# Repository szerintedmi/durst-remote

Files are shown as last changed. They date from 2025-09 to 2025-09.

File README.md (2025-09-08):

# Durst Laborator 1200 — Wireless Display and Control

Retrofitted display and control for the Durst Laborator 1200 enlarger.

Controls:

- Motor up/down (normal or fast)
- Lens up/down (normal or fast)
- Lamp on/off or by timer

Control via:

- TM1638 panel (8 buttons)
- Bluetooth gamepad

Displays:

- TM1638 7‑segment
- Grove LCD (16×2 characters)

Either display can be wired to the master module or used wirelessly via a slave node over ESP‑NOW. The device also starts its own Wi‑Fi access point for setup, so you don’t need to join home Wi‑Fi to use the wireless display/panel.

## Overview

- Master node drives motors, lamp SSR, UI, and broadcasts display over ESP‑NOW.
- Slave node (optional) only renders the broadcasted display on TM1638/LCD.
- Brightness values: 0,1,2,7,OFF(255), persisted to NVS.

## Hardware/Pins (ESP32)

- TM1638: `STB=13`, `CLK=32`, `DIO=14` (high‑freq mode enabled).
- Buzzer: `GPIO16` (LEDC ch 4). Indicator LED disabled.
- Lamp SSR: `GPIO33`.
- Motor 1 (DRV8874): `IN1=25`, `IN2=26`, `CS=35`, `FAULT=27`, `SLEEP` tied HIGH, LEDC ch `0/1`.
- Motor 2 (DRV8874): `IN1=18`, `IN2=19`, `CS=34`, `FAULT=22`, `SLEEP` tied HIGH, LEDC ch `2/3`.

## Wiring

- Diagram: [KiCad/DurstControlRetrofitWiring.pdf](KiCad/DurstControlRetrofitWiring.pdf) or [KiCad/](KiCad/) (draft / work in progress) )
- For connecting the motors, the limit switches and lamp to the right cables see [Durst Service manuals](http://durst.loremi.com/).
- Slave node: same wiring concept; only one or both displays (TM1638 and/or Grove LCD) need to be connected.

## Controls

TM1638 panel (controls only if TM1638 is connected to master):

- `S1` Fast speed (motors or timer adjust)
- `S1+S8` toggle lamp (on/off)
- `S2` timer −0.1s; `S3` timer +0.1s
- `S1+S2` timer -1s; `S1+S3` timer +1s
- `S4` M1 down; `S5` M1 up
- `S6` M2 down; `S7` M2 up
- `S8` start / cancel timer
- Conflicts (e.g., up+down) coast + short beep.

Bluetooth gamepad (Bluepad32):

- `Cross(×)` / `Triangle(△)`: M1 (Head) up/down
- `Square(□)`  /  `Circle(○)` : M2 (Lens) up/down
- Fast motor Speed: `L2`/`R2`,  Insane `L1`
- Timer adjust +/-0.1s: D‑pad Up/Down
- Timer +/-1s: `L2`/`R2` + Dpad Up/Down
- Timer +/-10s: `L1` + Dpad Up/Down
- Start / cancel lamp with timer:  D-Pad Right
- Toggle lamp: D-Pad Left
- Adjust TM1638 Display Brightness: `R1`

## Display & Feedback

- TM1638 text shows the active motor duty or `ERRn`, plus lamp and timer (e.g., `123L  4.5`).
- LCD line 1/2 show a short status and timer; LEDs mirror the buttons mask.
- Display state is broadcast over ESP‑NOW; slaves render the same UI.

## Motor Driver (DRV8874)

- FreeRTOS tasks: duty control (500 Hz) and current sense averaging (up to 100 Hz).
- Active brake: both IN high for a short window, then coast.
- Min duty per direction allows asymmetric thresholds; ADC uses 11 dB attenuation.

## Buzzer

- LEDC‑based tone with one‑shot `esp_timer` auto‑stop. Used on conflict/fault.

## Wi‑Fi, ESP‑NOW & Web UI

- Starts SoftAP and attempts STA using saved creds.
- Endpoints: `GET /wifi/api/status`, `POST /wifi/save`, `POST /wifi/reset`.
- UI: `/index.html` (quick), `/wifi/index.html` (detailed+config).
- ESP‑NOW mesh is initialized; broadcast peer is pre‑added. Display messages use `MsgV1`.

## Build & Flash (PlatformIO)

- Master (default): `pio run -e esp32dev` → upload with `-t upload`.
- Slave (display‑only): `pio run -e esp32slave` → upload with `-t upload`.
- LittleFS: `pio run -t buildfs` and `pio run -t uploadfs`.

Notes: see [platformio.ini](platformio.ini) for board, ports, Bluepad32 framework package, and the pre‑build gzip step ([tools/gzip_fs.py](tools/gzip_fs.py)).

## Repo Layout

- [src/](src/) — [mainMaster.cpp](src/mainMaster.cpp) (master), [mainSlave.cpp](src/mainSlave.cpp) (slave).
- [lib/DRV8874/](lib/DRV8874/) — motor driver and control tasks.
- [lib/Controls/](lib/Controls/), [lib/GamePad/](lib/GamePad/) — input merge and Bluepad32 wrapper.
- [lib/DisplayMux/](lib/DisplayMux/), [lib/TM1638plusWrapper/](lib/TM1638plusWrapper/) — display + broadcast.
- [lib/WifiPortal/](lib/WifiPortal/) — SoftAP/STA, routes, ESP‑NOW init.
- [data_src/](data_src/) → [data/](data/) — web UI, gzipped at build.

## Mesh Password

- default password used for the mesh SoftAP is `changeme`
- Create `include/secrets.h` in [include/](include/) and add `#define MESH_PASS yourpassword` to customize.
- `include/secrets.h` is already in [.gitignore](.gitignore)

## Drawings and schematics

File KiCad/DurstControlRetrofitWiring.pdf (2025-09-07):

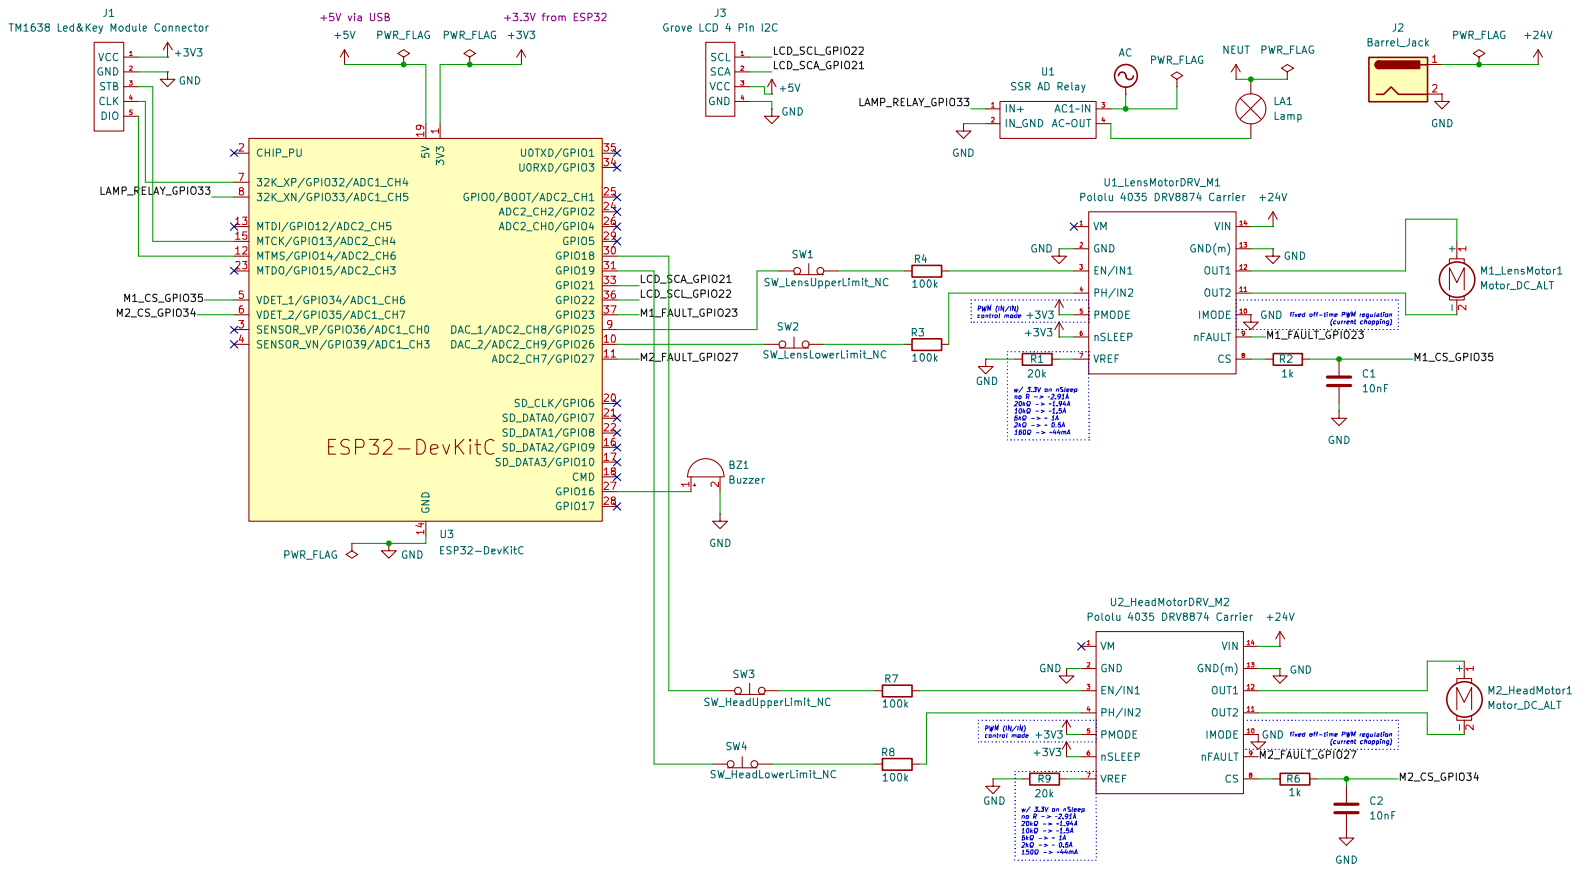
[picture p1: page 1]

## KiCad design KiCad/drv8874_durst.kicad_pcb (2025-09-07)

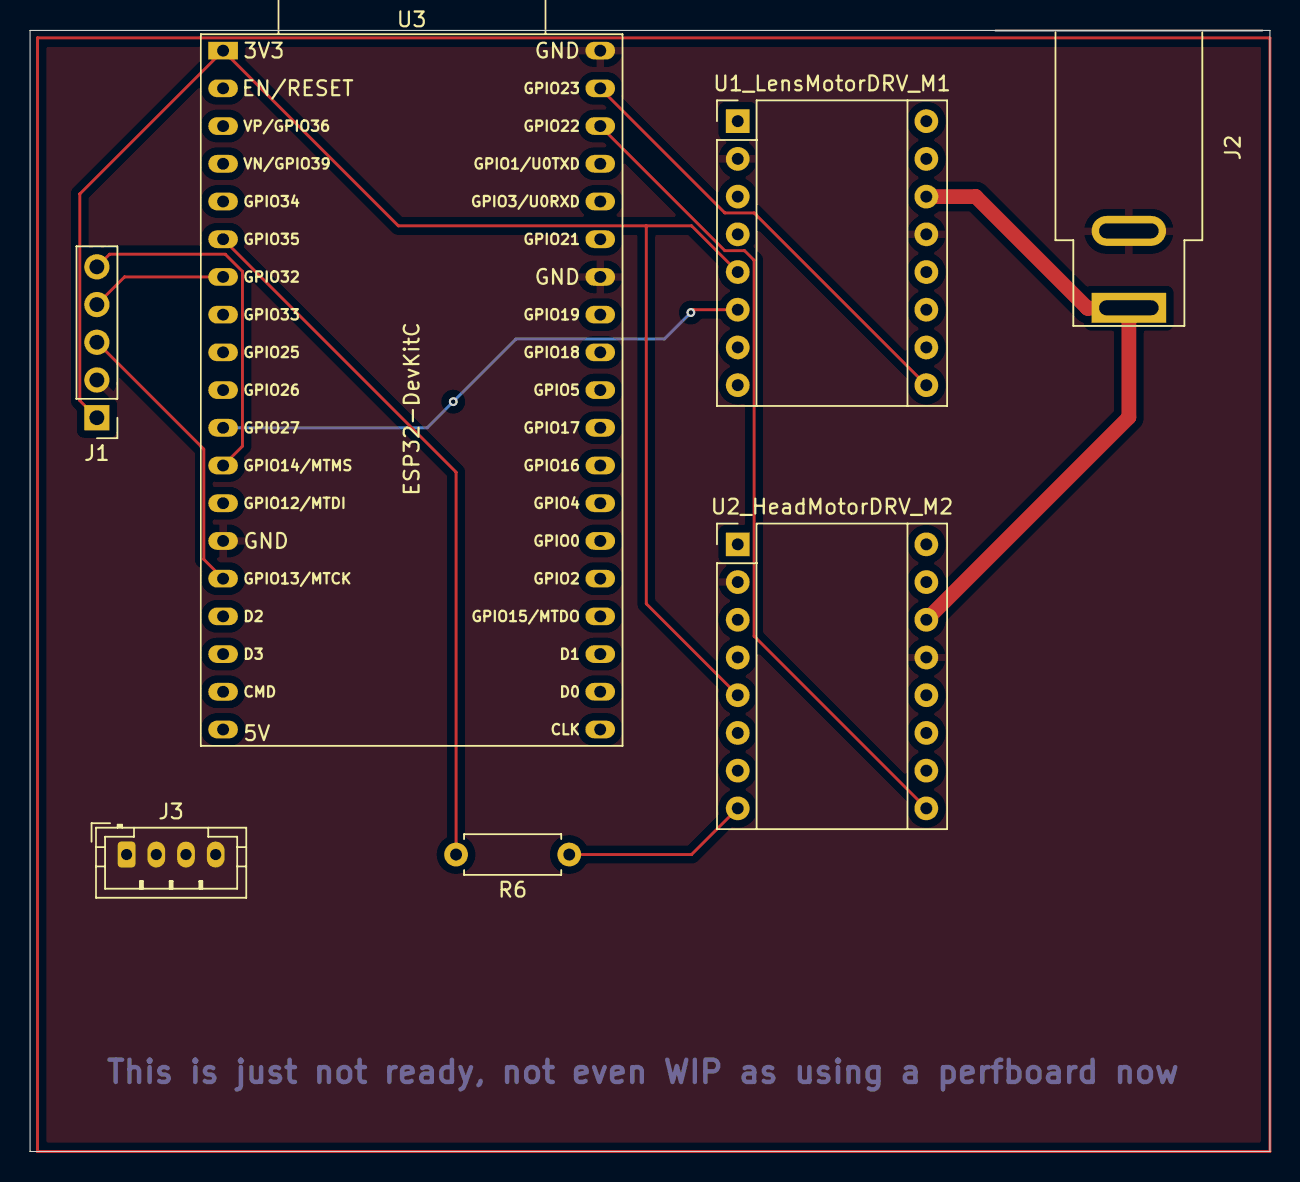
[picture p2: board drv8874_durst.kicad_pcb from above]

Board: 2 copper layers, 83.5 x 75.5 mm, 7 parts (0 on the bottom side), 13 nets.

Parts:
J1: TM1638 Led&Key Module Connector; PinHeader_1x05_P2.54mm_Vertical
J2: Barrel_Jack; BarrelJack_SwitchcraftConxall_RAPC10U_Horizontal
J3: Grove LCD 4 Pin I2C; JST_PH_B4B-PH-K_1x04_P2.00mm_Vertical
R6: 1k; R_Axial_DIN0207_L6.3mm_D2.5mm_P7.62mm_Horizontal
U1_LensMotorDRV_M1, U2_HeadMotorDRV_M2: Pololu 4035 DRV8874 Carrier; Pololu_Breakout-16_15.2x20.3mm
U3: ESP32-DevKitC

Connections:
+3V3: J1.1 (VCC), U1_LensMotorDRV_M1.5 (PMODE), U1_LensMotorDRV_M1.6 (nSLEEP), U2_HeadMotorDRV_M2.5 (PMODE), U2_HeadMotorDRV_M2.6 (nSLEEP), U3.1 (3V3)
+5V: J3.3 (VCC), U3.19 (5V)
+24V: J2.1, U1_LensMotorDRV_M1.14 (VIN), U2_HeadMotorDRV_M2.14 (VIN)
/LCD_SCA_GPIO21: J3.2 (SCA), U3.33 (GPIO21)
/LCD_SCL_GPIO22: J3.1 (SCL), U3.36 (GPIO22)
/M1_FAULT_GPIO23: U1_LensMotorDRV_M1.9 (nFAULT), U3.37 (GPIO23)
/M2_CS_GPIO34: R6.2, U3.6 (VDET_2/GPIO35/ADC1_CH7)
/M2_FAULT_GPIO27: U2_HeadMotorDRV_M2.9 (nFAULT), U3.11 (ADC2_CH7/GPIO27)
GND: J1.2 (GND), J2.2, J3.4 (GND), U1_LensMotorDRV_M1.2 (GND), U1_LensMotorDRV_M1.10 (IMODE), U1_LensMotorDRV_M1.13 (GND(m)), U2_HeadMotorDRV_M2.2 (GND), U2_HeadMotorDRV_M2.10 (IMODE), U2_HeadMotorDRV_M2.13 (GND(m)), U3.14 (GND), U3.32 (GND), U3.38 (GND)
unnamed: J1.4 (CLK), U3.7 (32K_XP/GPIO32/ADC1_CH4)
unnamed: J1.5 (DIO), U3.12 (MTMS/GPIO14/ADC2_CH6)
unnamed: J1.3 (STB), U3.15 (MTCK/GPIO13/ADC2_CH4)
unnamed: R6.1, U2_HeadMotorDRV_M2.8 (CS)

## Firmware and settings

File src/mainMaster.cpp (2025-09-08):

#include <Arduino.h>
#include <Preferences.h>
#include <WiFi.h>
#include <esp_wifi.h>
#include <esp_now.h>
#include <ESPAsyncWebServer.h>
#include <LittleFS.h>
#include <rgb_lcd.h>

#include "SimpleTimer.h"
#include "WifiPortal.h"
#include "TM1638plusWrapper.h"
#include "DisplayMux.h"
#include "DRV8874.h"
#include "Buzzer.h"
#include "Controls.h"
#include "SimpleRelay.h"

Preferences prefs;

SimpleTimer timer(9000);

// Lamp SSR relay (declare before onTimerDone)
constexpr uint8_t LAMP_RELAY_PIN = 33;
SimpleRelay lamp(LAMP_RELAY_PIN);

static void onTimerDone(void *ctx)
{
  lamp.off();
  Serial.println("Timer finished!");
}

// ================= TM1638 setup =================
constexpr uint8_t TM1638_CLK_PIN = 32;
constexpr uint8_t TM1638_DIO_PIN = 14;
constexpr uint8_t TM1638_STB_PIN = 13;
constexpr bool IS_TM1638_HIGH_FREQ = true; // default false,, If using a high freq CPU > ~100 MHZ set to true.

// TM1638
uint8_t brightness = 0;
TM1638plusWrapper tm(TM1638_STB_PIN, TM1638_CLK_PIN, TM1638_DIO_PIN, IS_TM1638_HIGH_FREQ);

// Grove LCD Display , defaults to PIN 21 SDA and 22 SCL
rgb_lcd lcd; // default pins 21 and 22
DisplayMux displays(&tm, &lcd);

// Lamp SSR relay handled above

// ================= Buzzer =================
constexpr uint8_t BUZZER_PIN = 16; // your buzzer GPIO
constexpr uint8_t LEDC_CH = 4;     // LEDC channel you want to use
constexpr int8_t LED_PIN = -1;     // optional LED; or -1 to disable

Buzzer buzz(BUZZER_PIN, LEDC_CH, LED_PIN);

// ================= TWO motors =================

// We assume PWM (IN/IN) mode , i.e. PMODE is tied HIGH on the hardware
constexpr uint8_t M1_IN1 = 25;
constexpr uint8_t M1_IN2 = 26;
constexpr uint8_t M1_SLEEP = 0; // if hard-wired HIGH, set to 0
constexpr uint8_t M1_FAULT = 27;
constexpr uint8_t M1_CS = 35;
constexpr uint8_t M1_CH1 = 0;
constexpr uint8_t M1_CH2 = 1;

constexpr uint8_t M2_IN1 = 18;
constexpr uint8_t M2_IN2 = 19;
constexpr uint8_t M2_SLEEP = 0; // if hard-wired HIGH, set to 0
constexpr uint8_t M2_FAULT = 27;
constexpr uint8_t M2_CS = 34;
constexpr uint8_t M2_CH1 = 2;
constexpr uint8_t M2_CH2 = 3;

// Motor minDuty set to result a duty where the motor moving when speedPt set to 10%
// Lens motor min duty down 613 , up 640. w/ 10% speed minDutyPos = 568,  minDutyNeg = 598
DRV8874 motor1(M1_IN1, M1_IN2, M1_CS, M1_SLEEP, M1_CH1, M1_CH2,
               568 /* minDutyPos */, 598 /* minDutyNeg */);
// Head motor min duty down 628, up 623. w/ 10% speed minDutyPos = 584,  minDutyNeg = 579
DRV8874 motor2(M2_IN1, M2_IN2, M2_CS, M2_SLEEP, M2_CH1, M2_CH2,
               584 /* minDutyPos */, 579 /* minDutyNeg */);

void updateDisplay(const uint8_t brightness, const bool lampState, const DRV8874 &m1, const DRV8874 &m2, const SimpleTimer &timer,
                   const bool anyDirectionConflict, const bool m1Fault, const bool m2Fault)
{
  char segText[11] = "";                  // 2x4 chars + optional 2 x 1 decimal point + NUL for TM1638plus::displayText
  char lcdLine1[17] = "I'm the master!!"; // 16 chars + NUL. Slave ignores lcdLine1 and overrides with debug info
  char lcdLine2[17] = "";

  const int32_t m1Signed = m1.getDutyCmd() * m1.getDirection();
  const int32_t m2Signed = m2.getDutyCmd() * m2.getDirection();
  const uint32_t timerMs = static_cast<uint32_t>(timer.remainingMs());
  uint16_t tenths = (timerMs + 50) / 100; // round to 0.1s
  uint16_t whole = tenths / 10;
  uint8_t frac = tenths % 10;

  // Choose which value to display: prefer M1 unless it is zero
  int32_t toDisplay = (m1Signed == 0 ? m2Signed : m1Signed);
  int32_t toDisplayClamped = toDisplay < -999 ? -999 : toDisplay; // we only have 4 digits on the TM1638

  int8_t errorCode = m1Fault ? 1 : m2Fault            ? 2
                               : anyDirectionConflict ? 3
                                                      : 0;

  int firstSeg = errorCode ? errorCode : (int)toDisplayClamped;
  const char lampStateChar = lampState ? 'L' : ' ';

  snprintf(segText, sizeof(segText),
           errorCode ? "ERR%1d%3u.%u" : "%4d%1c%2u.%u",
           firstSeg, lampStateChar, (unsigned)whole, (unsigned)frac);

  snprintf(lcdLine2, sizeof(lcdLine2),
           errorCode ? "ERROR:%1d  %4u.%us" : "%5d    %1c%3u.%us",
           errorCode ? errorCode : (int)toDisplay, lampStateChar, (unsigned int)whole, frac);

  displays.displayAndBroadCastTexts(brightness, segText, lcdLine1, lcdLine2);
}

// Controls handled by Controls module

volatile bool faultM1 = false;
void IRAM_ATTR onM1Fault() { faultM1 = true; }
volatile bool faultM2 = false;
void IRAM_ATTR onM2Fault() { faultM2 = true; }

// ================= Web server & WifiPortal =================

AsyncWebServer webServer(80);
WifiPortal wifiPortal(MESH_SSID, MESH_PASS);

static void attachRoutes()
{
  if (!(LittleFS.begin(false) || LittleFS.begin(true))) // idempotent
  {
    Serial.println("LittleFS mount failed");
    return;
  }

  webServer.serveStatic("/", LittleFS, "/")
      .setDefaultFile("index.html")
      .setFilter([](AsyncWebServerRequest *r)
                 {
                const String& u = r->url();
                return !(u.startsWith("/wifi/api/") || u == "/wifi/api"); });

  ;
}

// ================= Setup =================
void setup()
{
  Serial.begin(115200);

  lamp.begin(); // default initial state: OFF

  attachRoutes();
  wifiPortal.beginAndConnect(webServer, /*staTimeoutMs=*/10000);
  webServer.begin();

  buzz.begin();

  prefs.begin("durst", false);

  timer.setDurationMs(prefs.getULong("duration", 9)); // set last used duration

  // ---- TM1638 and Grove LCD Display init (optional hardware) ----
  // Same default pins as slave; disable
  brightness = prefs.getUChar("brightness", 7);
  displays.begin(brightness); // initializes TM1638 if present
  displays.setBroadcastEnabled(true);

  Serial.printf("Setup(): brightness=%d\n", brightness);

  analogReadResolution(12);
  // Set default attenuation for all ADC reads. Per-pin attenuation before
  // first read can log errors on ESP32 Arduino v3.x, so avoid that here.
  analogSetAttenuation(CS_ADC_ATTENUATION);

  motor1.begin();
  pinMode(M1_FAULT, INPUT_PULLUP); // or INPUT with external 10k
  attachInterrupt(digitalPinToInterrupt(M1_FAULT), onM1Fault, FALLING);

  motor2.begin();
  pinMode(M2_FAULT, INPUT_PULLUP); // or INPUT with external 10k
  attachInterrupt(digitalPinToInterrupt(M2_FAULT), onM2Fault, FALLING);

  // ---- Controls (TM1638 + controller using BluePad32) ----
  Controls::begin(&tm);

  Serial.println("Setup: done");
}

void loop()
{
  // unsigned motorspeed in % of MAX_DUTY
  constexpr uint8_t SLOW_PT = 10;
  constexpr uint8_t FAST_PT = 70;
  constexpr uint8_t INSANE_PT = 100;

  // Update controls (merges TM1638 + BT) and fetch state
  Controls::update();
  const auto &cs = Controls::state();
  if (motor1.getDutyCmd() > 0 || motor2.getDutyCmd())
    Serial.printf(">m1DutyCmd:%d,m2DutyCmd:%d,m1A:%.2f,m2A:%.2f,\r\n",
                  motor1.getDutyCmd(), motor2.getDutyCmd(), motor1.getCurrentmA() / 1000.0f, motor2.getCurrentmA() / 1000.0f);

  uint8_t speedControlPt = cs.Fast ? FAST_PT : cs.Insane ? INSANE_PT
                                                         : SLOW_PT;

  // TODO: race conditions? also, do we need debounce?
  bool debouncedFaultM1 = false;
  bool debouncedFaultM2 = false;
  if (faultM1)
  {
    delayMicroseconds(200);
    if (digitalRead(M1_FAULT) == LOW) // small debounce/filter in case of brief pulses
      debouncedFaultM1 = true;
  }

  if (faultM2)
  {
    delayMicroseconds(200);
    if (digitalRead(M2_FAULT) == LOW) // small debounce/filter in case of brief pulses
      debouncedFaultM2 = true;
  }

  // Motor 1 command
  if (cs.m1Conflict || debouncedFaultM1)
  {
    motor1.coast();
    buzz.buzz(200, 255, 80);
  }
  else if (cs.m1Dir == 0 && motor1.getSpeed() != 0)
    // motor1.coast();
    motor1.brake();
  else if (motor1.getSpeed() != speedControlPt * cs.m1Dir)
  {
    motor1.run(speedControlPt * cs.m1Dir);
  }

  // Motor 2 command
  if (cs.m2Conflict || debouncedFaultM2)
  {
    motor2.coast();
    buzz.buzz(200, 255, 80);
  }
  else if (cs.m2Dir == 0 && motor2.getSpeed() != 0)
    // motor2.coast();
    motor2.brake();
  else if (motor2.getSpeed() != speedControlPt * cs.m2Dir)
  {
    motor2.run(speedControlPt * cs.m2Dir);
  }

  displays.segSetLEDs(cs.buttonsMask);

  if (Controls::rising(&ControlsState::Brightness))
  {
    brightness = TM1638plusWrapper::getNextBrightness(brightness); // updateDisplay will take care of it
    prefs.putUChar("brightness", brightness);
    Serial.printf("mainMaster: new brightness=%d\n", brightness);
  }

  // Start timer on rising edge only (avoid restart every loop while pressed)
  if (Controls::rising(&ControlsState::StartTimer))
  {
    if (lamp.isOn() && timer.isRunning())
    {
      lamp.off();
      timer.stop();
      Serial.println("mainMaster: Timer cancel (timer was running and lamp was on)");
    }
    else
    {
      prefs.putULong("duration", timer.getDurationMs()); // save last used duration for next boot
      timer.start(onTimerDone);
      lamp.on();
      Serial.printf("mainMaster: Timer started timer.remainingMs()=%d timer.isRunning()=%d timer.getDurationMs()=%d\n",
                    (int)timer.remainingMs(), (int)timer.isRunning(), (int)timer.getDurationMs());
    }
  }

  if (Controls::rising(&ControlsState::toggleLamp))
  {
    lamp.toggle();
    Serial.printf("toggleLamp: lamp is now %s\n", lamp.isOn() ? "ON" : "OFF");
  }

  if (!timer.isRunning()) // ignore timer adjusment while it's running
  {
    uint16_t timerStep = 100;
    if (cs.Fast)
      timerStep = 1000;
    else if (cs.Insane)
      timerStep = 10000;

    // Apply timer +/- no faster than every repeatMs while button is held
    static uint32_t nextTimerAdjustMs = 0; // 0 means immediate on next press
    const uint16_t repeatMs = 200;         // adjust rate while holding (ms)
    const uint32_t nowMs = millis();
    const bool anyTimerAdjust = cs.decreaseTimer || cs.increaseTimer;

    if (anyTimerAdjust && (nowMs >= nextTimerAdjustMs))
    {
      uint32_t newDuration = timer.getDurationMs();

      if (cs.decreaseTimer)
      {
        if (newDuration <= timerStep)
          newDuration = 100ULL;
        else
          newDuration -= timerStep;
      }
      else if (cs.increaseTimer)
      {
        if (newDuration + timerStep > 9999000ULL)
          newDuration = 9999000ULL;
        else
          newDuration += timerStep;
      }
      Serial.printf("Adjusting timer. Current: %lu ms  New: %lu ms\n", timer.getDurationMs(), newDuration);
      timer.setDurationMs(newDuration);
      nextTimerAdjustMs = nowMs + repeatMs; // schedule next repeat
    }
    else if (!anyTimerAdjust)
    {
      nextTimerAdjustMs = 0; // reset so next press acts immediately
    }
  }

  updateDisplay(brightness, lamp.isOn(), motor1, motor2, timer, cs.anyDirectionConflict, debouncedFaultM1, debouncedFaultM2);

  delay(10);
}

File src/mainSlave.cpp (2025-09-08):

// Minimal slave node: joins same WiFi/ESP-NOW mesh and prints display messages
#include <Arduino.h>
#include <WiFi.h>
#include <esp_wifi.h>
#include <esp_now.h>
#include <rgb_lcd.h>
#include <esp_log.h>

// For detecting IDF version to select correct ESP-NOW callback signature
#if __has_include(<esp_idf_version.h>)
#include <esp_idf_version.h>
#else
// Fallback if header not available (treat as older core)
#define ESP_IDF_VERSION_VAL(major, minor, patch) 0
#define ESP_IDF_VERSION 0
#endif

#include "DurstProto.h"
#include "TM1638plusWrapper.h"
#include "DisplayMux.h"

// TM1638 pins (same defaults as master)
constexpr uint8_t TM1638_CLK_PIN = 32;
constexpr uint8_t TM1638_DIO_PIN = 14;
constexpr uint8_t TM1638_STB_PIN = 13;
constexpr bool IS_TM1638_HIGH_FREQ = true;

// ---- TM1638 Display and/or Grove LCD Display ----
// Same default pins as master; harmless if no board attached
TM1638plusWrapper tm(TM1638_STB_PIN, TM1638_CLK_PIN, TM1638_DIO_PIN, IS_TM1638_HIGH_FREQ);
rgb_lcd lcd;
DisplayMux displays(&tm, &lcd); // not broadcasting (disbaled by default)

static uint32_t lastBroadcastedSeq = 0;
static uint32_t lastBroadcastReceivedMs = 0;
static bool isConnected = false;
static uint32_t broadcastLostCount = 0;

// TODO: same vars in DisplayMux just not maintained when not broadcasting. Consider using those and remove these
uint8_t lastBroadcastedSegBrightness_ = DEFAULT_SEG_BRIGHTNESS;
char lastBroadcastedSegText_[11] = "";
char lastBroadcastedLcdLine1_[17] = "";
char lastBroadcastedLcdLine2_[17] = "";

// Helper to get debug line for display
const char *getDebugLine()
{
  static char line1OverrideForDebug[17] = {0};
  snprintf(line1OverrideForDebug, sizeof(line1OverrideForDebug), "%5d  lost:%4d", lastBroadcastedSeq, broadcastLostCount);
  return line1OverrideForDebug;
}

// ESP-NOW recv callback signature changed in IDF 5/Arduino-ESP32 v3.x
// - New: onEspNowRecv(const esp_now_recv_info_t *info, const uint8_t *data, int len)
// - Old: onEspNowRecv(const uint8_t *mac_addr, const uint8_t *data, int len)
static void onDisplayBroadcast(const MsgV1 &m)
{
  const MsgV1 *msg = &m;

  // TODO: hasAnyChanged here is only for debugging also duplicate of logic in DisplayMux::broadcastIfDue
  const bool hasAnyChanged =
      (msg->brightness != lastBroadcastedSegBrightness_) ||
      (memcmp(msg->segText, lastBroadcastedSegText_, sizeof(msg->segText)) != 0) ||
      (memcmp(msg->lcdLine1, lastBroadcastedLcdLine1_, sizeof(msg->lcdLine1)) != 0) ||
      (memcmp(msg->lcdLine2, lastBroadcastedLcdLine2_, sizeof(msg->lcdLine2)) != 0);

  if (lastBroadcastedSeq > msg->seq)
  {
    Serial.printf("onEspNowRecv: Likely master restart - out of order seq: %d last_broadcast_seq: %d\n", msg->seq, lastBroadcastedSeq);
    lastBroadcastedSeq = 0;
    broadcastLostCount = 0;
  }
  else if (lastBroadcastedSeq != 0 && msg->seq != lastBroadcastedSeq + 1)
  {
    uint32_t lost_count = msg->seq - lastBroadcastedSeq - 1;
    broadcastLostCount += lost_count;
    Serial.printf("onEspNowRecv: lost %d messages. lastBroadcastedSeq: %d current seq: %d Total lost: %d\n",
                  lost_count, lastBroadcastedSeq, msg->seq, broadcastLostCount);
  }

  displays.displayAndBroadCastTexts(msg->brightness, msg->segText, getDebugLine(), msg->lcdLine2);

  lastBroadcastedSeq = msg->seq;
  lastBroadcastedSegBrightness_ = msg->brightness;
  lastBroadcastReceivedMs = millis();
  isConnected = true;
  memcpy(lastBroadcastedSegText_, msg->segText, sizeof(msg->segText));
  memcpy(lastBroadcastedLcdLine1_, msg->lcdLine1, sizeof(msg->lcdLine1));
  memcpy(lastBroadcastedLcdLine2_, msg->lcdLine2, sizeof(msg->lcdLine2));

  displays.displayAndBroadCastTexts(msg->brightness, msg->segText, getDebugLine(), msg->lcdLine2);

  if (hasAnyChanged)
  {
    Serial.printf("onEspNowRecv: text / brightness changed seq=%lu brightness=%d segText='%s' lcdLine1='%s' lcdLine2='%s' lcdLine1OverrideForDebug='%s'\n",
                  (unsigned long)msg->seq, msg->brightness, msg->segText, msg->lcdLine1, msg->lcdLine2, getDebugLine());
  }
}

void onConnectionLost()
{
  isConnected = false;
  displays.displayAndBroadCastTexts(lastBroadcastedSegBrightness_, "Conn.LOSt",
                                    getDebugLine(), "Connection lost ");

  Serial.println("mainSlave.onConnectionLost: Connection lost to master");
}

void setup()
{
  Serial.begin(115200);

  displays.begin();

  Serial.println("[SLAVE] Joining mesh...");
  displays.displayAndBroadCastTexts(lastBroadcastedSegBrightness_, "BOOTING ",
                                    getDebugLine(), "Booting...   ");

  // Configure STA
  WiFi.mode(WIFI_STA);
  esp_wifi_set_ps(WIFI_PS_NONE);
  WiFi.setAutoReconnect(true);
  WiFi.persistent(false);
  // WiFi.begin(MESH_SSID, MESH_PASS); don't need for mesh mode (using onyl softAP) and connecting to AP is slow to connect and would require to manage channel changes

  // Init ESP-NOW (will be ready regardless of STA state)
  if (esp_now_init() == ESP_OK)
  {
    uint8_t pri = 0;
    wifi_second_chan_t sec = WIFI_SECOND_CHAN_NONE;
    esp_wifi_get_channel(&pri, &sec);
    Serial.printf("[SLAVE] STA ESP NOW INIT SUCCESS. Wifi Channel: %d. esp channel: %d\n", WiFi.channel(), pri);
    DurstProto::setOnDisplayBroadcast(&onDisplayBroadcast);
    displays.displayAndBroadCastTexts(lastBroadcastedSegBrightness_, "CONNECT ",
                                      getDebugLine(), "Connecting...   ");
  }
  else
  {
    displays.displayAndBroadCastTexts(lastBroadcastedSegBrightness_, "ESP-ERR ",
                                      getDebugLine(), "ESPNow init fail");
    Serial.println("[SLAVE] ESP-NOW init failed");
  }
}

void loop()
{
  if (millis() - lastBroadcastReceivedMs > 2000 && isConnected)
    onConnectionLost();

  delay(300); // long delay is fine until we only check for lost connection in loop
}

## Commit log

2025-09-08 change M2Fault pin to 27 so lcd can be connected too
2025-09-08 cancel timer w/ DPad right. Timer +/- 10s with L1+PadUp/Down. Ignore adjust while running
2025-09-13 kicad : add relay
    [drv8874_durst.kicad_sch]
